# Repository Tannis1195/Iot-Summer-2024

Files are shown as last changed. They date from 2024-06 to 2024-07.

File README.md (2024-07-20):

# Tutorial on how to build an automatic plant watering system
Jonathan Lannerås (jl225yi) planned and carried out this project in June 2024.

This project is based on Raspberry Pi pico WH which reads the current soil moisture of two different plants and pumps water from a reservoir when the soil gets too dry. In addition to this, it measures: Room temperature, Sunlight, Room Humidity, and current water level in the reservoir and uploads it to an Adafruit.io dashboard through Wifi. The system is powered by a 4000mAh power bank and a 1000mAh solar-rechargeable power bank, providing a total of approximately 5000mAh and recharging when exposed to sunlight. 

While the project was completed over three weeks with sporadic effort, an average person with a basic understanding of programming and electronics could likely complete it in approximately 10 hours.

## Objective
Are you the type of person who most often forgets that plants need water? Turns out that I am, and sadly one too many cactuses has not lived to tell the tale. In plain text I'm horrible at ensuring that my green friends get the care and attention they deserve (And desperately need), therefore, it was more than time to automate myself out of the equation and give the plants a fair chance. Although this project has not dwelled as deep into network security as I initially had hoped, it has given me a lot of new insights into the realm of home automation and also gained a fascination with the relative simplicity and cheapness of deploying small IoT projects for home improvements.

The way the system is intended to work is depicted in the flowchart below: 
<div align="center">
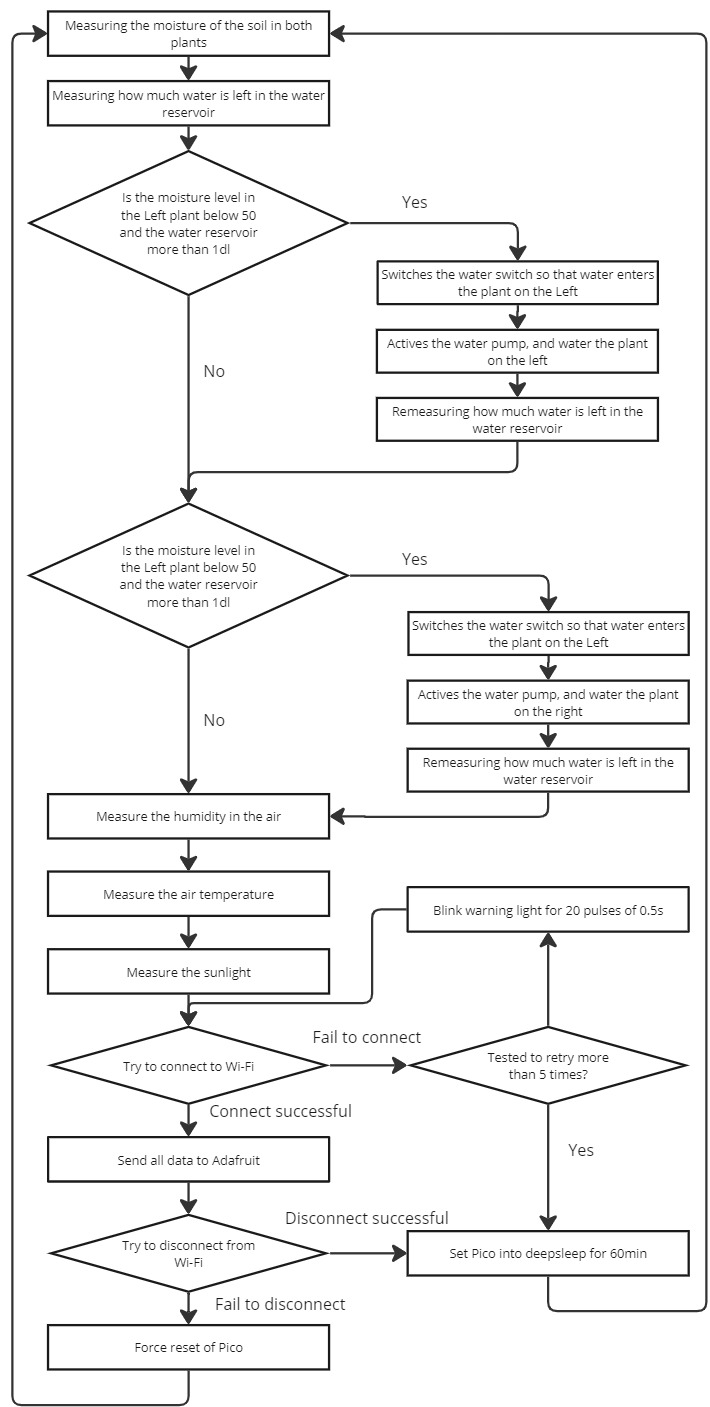
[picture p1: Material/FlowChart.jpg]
	
</div>

As seen in the flowchart the system consists of several parts and aims to both collect relevant data points, as well as continuously water the plants as needed. 

## Material

| Quantity | Component/Link | Use Case | Price (SEK) |
|---|---|---|---|
| Numerous | Just a random mix-match of childhood legos | Used to build the structure of the system | - |
| 1 | Just a large container to use as the water reservoir | Used as a water reservoir | - |
| 1 | [Male-male Wires](https://www.electrokit.com/kopplingstrad-byglar-for-kopplingsdack-mjuka-65st) | Used to connect components | 39 |
| 1 | [Male-female Wires](https://www.electrokit.com/labsladd-1-pin-hane-hona-150mm-10-pack) | Used to connect components | 29 |
| 1 | [Raspberry Pi Pico WH](https://www.electrokit.com/raspberry-pi-pico-wh) | The microcontroller used to handle all logic of the system | 109 |
| 1 | [Micro servo TS90 / SG90 1.2 kg](https://www.electrokit.com/micro-servo-ts90-sg90-1.2kg) | Micro servo used to control the water switch | 49 |
| 1 | [DHT11 Sensor](https://www.electrokit.com/digital-temperatur-och-fuktsensor-dht11) | Used to measure temperature and humidity | 49 |
| 1 | [Powerbank Keep-Alive Device](https://www.electrokit.com/powerbank-keep-alive-device) | Used to keep the powerbank from shutting off | 49 |
| 2 | [Soil Moisture Sensor](https://www.electrokit.com/jordfuktighetssensor) | Used to measure the soil moisture of the plants | 58 (total)  |
| 1 | [Red LED](https://www.electrokit.com/led-5mm-rod-diffus-1500mcd) | Used as an alarm to signal that the system failed to connect to Wi-Fi | 5 |
| 1 | [Photoresistor](https://www.electrokit.com/fotomotstand-cds-4-7-kohm) | Used to measure light level | 8 |
| 1 | [Ultrasonic Distance Sensor](https://www.electrokit.com/avstandsmatare-ultraljud-hc-sr04-2-400cm) | Used to measure water level in the water reservoir  | 59 |
| 1 | [220 ohm Resistor](https://se.rs-online.com/web/p/through-hole-resistors/0131176?gb=s) | Used for a voltage divider alongside the photoresistor | 1 |
| 1 | [Breadboard](https://www.electrokit.com/kopplingsdack-840-anslutningar) | Used to connect the different components together | 69 |
| 1 | [Relay](https://www.electrokit.com/relakort-5v-opto-isolerat) | Used to control the water pump | 49 |
| 1 | [Water Pump](https://www.electrokit.com/drankbar-pump-3v) | Used to pump water from the reservoir to the plants (Mine is 5V, but could only find a 3V; I expect similar results) | 45 |
| 1 | [Battery Pack](https://www.electrokit.com/batterihallare-4xaa-box-brytare-sladd) | Used to power the water pump (The servo and the water pump could not be on the same circuit due to the servo acting up when the pump drew power) | 29 |
| 1 | [1000 mAh Rechargeable Powerbank](https://www.dormy.com/sv/varumarken/dormy/powerbank-solar-charger-14282044fik) | Used to recharge the main powerbank | 99 |
| 1 | [Just a standard no-brand 4000mAh powerbank](https://www.netonnet.se/art/hem-fritid/el-batterier/powerbank/on-powerbank-4000-mah-1a-blue/1032352.13728/) | Used to power the breadboard and all components connected to it | ~50 |

The total cost of the entire project is difficult to accurately estimate as most of the used parts are refurbished from old Aurdino starter packs, but after finding most parts (or similar) I have calculated an estimated cost of **~800 Sek**

## Computer setup
During this project, all MicroPython code was written in the Thonny IDE. I ran Thonny on a Surface Pro 7, which was connected to the Raspberry Pi Pico via its micro USB port. Here’s how I set it up:

1. Downloaded and installed [Thonny](https://thonny.org/)
2. Hold down the BOOTSEL button (Located on the pico) while connecting the Pico to the computer (This engaged BOOTLOADER mode)
3. Open Thonny
4. Click **Run**
5. Click **Select interpreter**
6. In the dropdown list choose **MicroPython (Raspberry Pi Pico)**
7. Click **Install or update firmware** and follow the directions given in the popup window
8. Press **OK** and you are good to go!

Note that it is mandatory to test out the software in the following way: 
1. Start a new **.py** file in Thonny
2. Enter the code: <br />
`print ("Hello World")`
3. Ensure that you are using the MicroPython (Raspberry Pi Pico) as your interpreter 
4. Run the code by pressing **Run current script**
5. If all went according to plan, you should expect a nice treat in the terminal :) 

As ample guides exist on how to get Micropython installed on a Raspberry Pi Pico, I will not cover it in greater detail in this tutorial! I can, however, recommend [How to Setup a Raspberry Pi Pico and Code with Thonny](https://www.youtube.com/watch?v=_ouzuI_ZPLs), which provides an excellent and detailed walkthrough! 
## Putting everything together
The development of the project went both very well and very badly at the same time which was not all that surprising. Large portions of time went into redesigning the wiring of the system to make it as clean as possible (when looking at the wiring later, take note that it was much worse earlier). I also rebuilt the Lego structure approximately five times as the testing of the system proved more demanding than anticipated. Furthermore, I spent countless hours debugging and testing the code to ensure functionality, a major timewaster was the sporadic behavior of the "Lightsleep" function, after some digging I learned that "Deepsleep" was the way to go. Lastly, I had to redo quite a bit of work as I learned that having the pump and servo connected to the same power source was unwise when the pump started the servo started as well (For some reason), and after some digging, I learned that servos need to be run on a pretty consistent line without power fluctuation. I therefore tried to connect the servo to an external power pack but it did not wanna work therefore I hooked the pump up to the external instead and kept the servo on the 5V on the breadbord and this worked fine. But despite these hick-up most of the development rolled on quite nicely after I had gotten a costume to the technologies, case-in-point was the dashboard which was finalized an hour after I had created my Adafruit account.

### Wiring 
The wiring diagram of the project is displayed below:
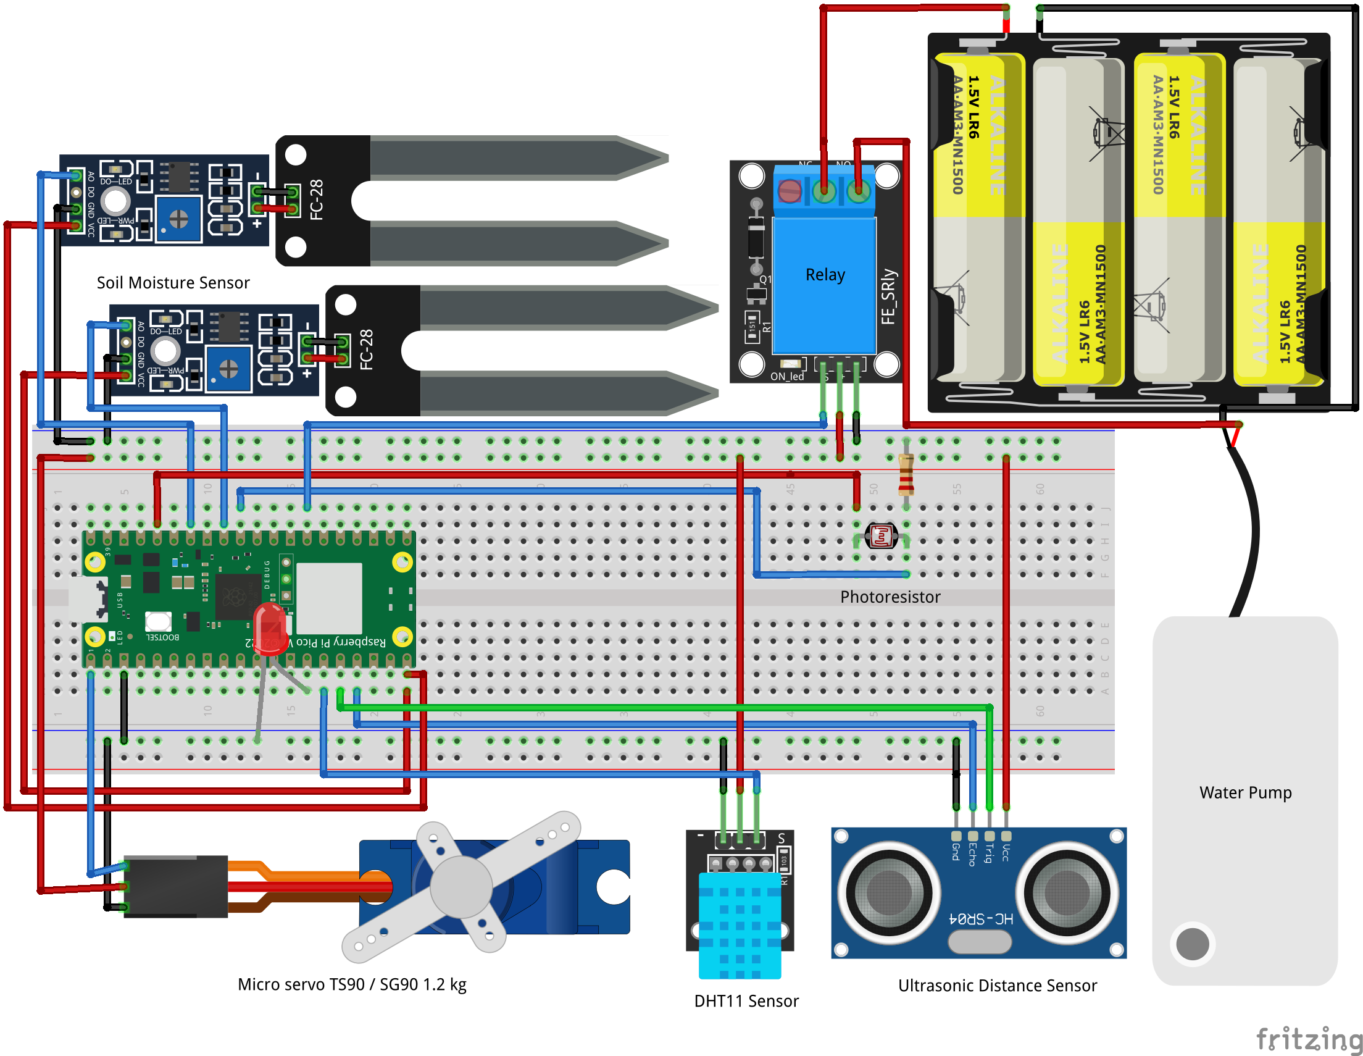
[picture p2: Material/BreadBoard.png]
Wireing diagram

In real life, this wiring is a tad bit more chaotic but it is all wired the same. The reason for my wiring work closely resembling a birds nest is that I lacked appropriate lengthed wires which led to a lot of suboptimal decisions, also the entire structure is built out of a miss match of old Lego I had laying around so the ability to plan and structure a sensible wiring approach was difficult. Thirdly, I'm also not that good at wiring so I'm certain that a more skilled practitioner who had access to the same supplies would have done more "presentable" work, but hey it works, and that's all that matters.
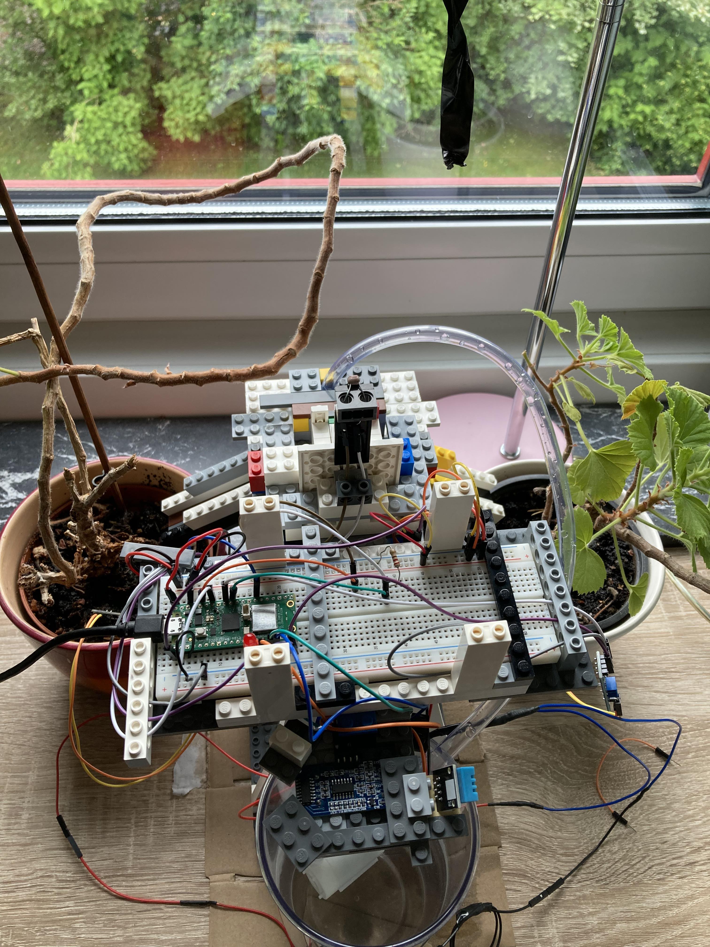
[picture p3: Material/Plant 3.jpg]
Wireing

### Power consumption 
Sadly, I could not get an accurate and long-term reading of power consumption, as I lacked access to the correct equipment. I tried to measure the current and voltage of the PICO using a multimeter and then calculate power consumption through (W = A*V), however, I was unable to get an accurate current reading of the PICO. I also tried measuring the power consumption through a wall-outlet power meter, this particular meter measures in KWh, and due to the fairly low consumption of the pico it was unable to get a reading. However, if we run some quick guesstimate for a day:

| Device | Operation Description | Duration | Current (mA) | Consumption (mAh) |
|---|---|---|---|---|
| Pico in Deepsleep | Pico in deepsleep mode (60 minutes between each of 24 readings) | 23 hours | 0.25 | 5.75 |
| Pico in action (With wifi on)  | Pico in operation (2-3 minutes for each of 24 instances) while wifi is on | 1 hour | 45 | 225 |
| Servo switch | Servo switch operation (1 activation) | 2 seconds | 500 | 0.278 |
| Water pump | Water pump operation (1 activation) | 1 second | 100 | 0.03 |
| Ultrasonic sensor HCSR0415 | Ultrasonic sensor operation (24 readings of water level) | 6 seconds | 15 | 0.025 |
| Powerbank Keep-Alive Device (active) | Powerbank wake-up pulse every 45 seconds | 192 seconds | 70 | 3.733 |
| Powerbank Keep-Alive Device (idle) | Powerbank idle state | ~24 hours | 1 | 23.947 |
| Soil moisture readings (per sensor) | Soil moisture sensor operation (24 readings per sensor) | 720 seconds | 15 | 3 (per sensor) |
| DHT11 sensor | DHT11 sensor operation (24 readings of temperature and humidity) | 2.4 seconds | 2.5 | 0.002 |

If we sum these estimates up we land at around 300 (~265) mAh per day. Given that I have around 5000 mAh in powerbank (without recharge) this indicates around 19 days of usage before having to recharge, which from experience seems probable but optimistic.     

## Platform 
In this project, all data is transmitted and stored in [Adafruit.io](https://io.adafruit.com/). My reasoning for choosing Adafruit instead of other options was based on two factors: Cost and ease of use. First of all, Adafruit is free to a limited extent and given the relatively low amounts of data I'm transmitting I was able to operate within these limits. Secondly, the ease of sending data to Adafruit using API made this a very attractive alternative as I'm familiar with how APIs work and was comfortable sending the data this way. Additionally, the way Adafruit has chosen to structure incoming data using different "feeds" which then can be used within dashboards was very straightforward and user-friendly, which was greatly appreciated on my part. It should, however, be noted that I found the free version of Adafruit to be quite limited in terms of data analytics and data representation but given the rather basic nature of the project, the need for either is close to non-existent. It would, however, have been neat to run a forecasting model on the data to determine when at what time the next refill of the water reservoir is bound to happen. This can of course be presumed offline by downloading the uploaded data from Adafruit and inputting it into analytical software such as **R** or **Python**. Additionally, using the free version of Adafruits services greatly impairs the scalability of the project as one is limited to 10 feeds in total, and currently the project is at 7 meaning that 3 additional plants could get added (Given that they are near the other plants) before one runs out of feeds.   <br />

Furthermore, my decision to use Adafruit in this project was also driven by the fact that I wanted to try out a cloud-based approach to IoT, and this project seemed like a good starting point. Why I deemed this project appropriate because of the fairly non-sense data I'm transmitting, for instance, I'm not transmitting live audio and video of my living room, because if this data leaks or gets intercepted the attacker will only gain some very detailed info about a mismanaged houseplant (and I can live with that).   
## The code
The core function within my code, the beating heart so to speak, is my main loop. The main loop executes my entire program and loops indefinitely, initially, the main loop addresses data collection and the watering functionalities of the system, after this the function shifts focus towards the uploading of the collected data to Adafruit. Not that if the program fails to connect to the internet, it will simply discard the collected data and enter deepsleep, this was an active choice of mine as the core functionality of the system is not the uploading of plant data to the internet, it is the ensuring of having the plants watered.   

```python
def main():
    while True:
        alarm_Pin.value(0) # Sets alarm pin to off 
        moist = plant_Monitor (sensorVCC,[left_Soil_Sensor,right_Soil_Sensor]) # Calculate the moisture level of the plants
        plant_Left_Moist_Level = moist[0]
        plant_Right_Moist_Level = moist[1]
        plants =[
            ["left",plant_Left_Moist_Level,50],
            ["right",plant_Right_Moist_Level,50]
        ]
        water_Level, watering = watering_Of_Plants(plants) # Calculates the water level in the water tank and investigates if the plants need to be watered   
        humidity_Temp = humidity_Temp_Tracker(25) # Calculates both Tempature and Humidity data
        temperature = humidity_Temp[0]
        humidity_Level = humidity_Temp[1]
        sun_Light = light_Tracker(50) # Calculates the current light level
        print("Moisture level of the Left plant: ", plant_Left_Moist_Level, "\n",
              "Moisture level of the Right plant: ", plant_Right_Moist_Level, "\n",
              "Temperature: ", temperature, "\n",
              "Humidity: ", humidity_Level, "\n",
              "Light Level: ", sun_Light, "\n",
              "Water Level: ", water_Level, "\n",
              "Watering events: ", watering)
         
        connected, wlan = connect_To_Wifi() # Try to connect to Wifi
        if connected:
            #Send data to Adafruit
            send_To_Adafruit(plant_Left_Moist_Level, "moisture-plant-1")
            plant_Left_Moist_Level=None #Delete from memory
            send_To_Adafruit(plant_Right_Moist_Level, "moisture-plant-2")
            plant_Right_Moist_Level=None #Delete from memory
            send_To_Adafruit(water_Level, "water-tank")
            water_Level=None #Delete from memory
            send_To_Adafruit(temperature, "temperature")
            temperature=None #Delete from memory
            send_To_Adafruit(humidity_Level, "humidity")
            humidity_Level=None #Delete from memory
            send_To_Adafruit(sun_Light, "sun-light")
            sun_Light=None #Delete from memory
            if len(watering) != 0: # If a watering event has been recorded
                for i in watering:
                    send_To_Adafruit(i,"watering-event")
                watering=None #Delete from memory
            wlan.disconnect() # Disconnect from WIFI
            time.sleep(1)
            if wlan.isconnected(): #If unable to disconnect
                print ("Disconnect has failed :(, It left me no choice")
                machine.reset() # Hard reset, im not allowing the pico to keep wifi on under any circumstance
            else:
                print("Great success, we have disconnected!")
                
        else: # If unable to connect to Wifi
           print("Connection was never an option :(, Data not delivered") # Data do not get uploaded or stored (Main objective is to ensure plant safety not Dashbord uplink)
           alarm_Pin.value(1) # Turn on alarm pin to indicate error
               
        deepsleep(60*60*1000)#Puts the pico into deepsleep for 60min
```
In all honesty, the majority of the code is centered around the collection of data from different sensors this is code that already has ample literature online and therefore is quite boring to address but I do have three codes that are a bit more interesting to look at.
### Deletion of outliers 
Albit, using a function that cleans the data from outliers is not a revolutionary concept nor unusual to include, the function is however usually imported from an established library rather than written. This was the first time I wrote such a function myself and it could be fun to share, especially as it is beyond important when dealing with sketchy wiring and sensors which are prone to throw out a strange value more often than not. The function incorporates linear interpolation when calculating the quartile values of Qurtial 1 and 2, these are then used to calculate the interquartile range and the lower and upper bounds. These bounds act as borders, any values beyond them are excluded leading to a clean dataset.   
```python
def outlier_Deleter(value_Array):
    value_Array = sorted(value_Array)
    n = len(value_Array)
    q1_Pos = (n + 1) / 4
    q3_Pos = 3 * (n + 1) / 4
    # This function is used to calculate the quartile values
    def qurtile_calc(pos):
        lower = value_Array[int(pos)-1]
        upper = value_Array[int(pos)]
        return lower + (pos%1)*(upper - lower)
    q1 = qurtile_calc(q1_Pos) # quartile 1
    q3 = qurtile_calc(q3_Pos)# quartile 1
    iqr = q3-q1# inter quartile range
    lower_Bound = q1 - (1.5*iqr)
    upper_Bound = q3 + (1.5*iqr)
    filtered_array = list(filter(lambda x:lower_Bound<=x<=upper_Bound,value_Array))
    return filtered_array
```

### Tracking Water level using an Ultrasonic Distance Sensor
This is the function used to determine the current level of water in my water reservoir/tank, it uses an Ultrasonic Distance Sensor mounted over the reservoir. It works by measuring the time it takes for a pulse to hit the water and then bound back to the Sensor, then converting this pulse time to get the gap between the sensor and water in centimeters. When the gap is determined I use this information to determine how much water I got in the reservoir, if there is no gap between water and sensor I got 9,4 dl and for every centimeter of the gap, the amount decreases by 0.56 DL meaning that when the gap is 16,8 cm the reservoir is empty!   
```python
def water_Level_Reader(sample_Size):
    result_Array = []
    for i in range(sample_Size):
        trig_SoundSensor.value(0)
        time.sleep(0.005)
        trig_SoundSensor.value(1)
        time.sleep(0.00001)
        trig_SoundSensor.value(0)
        pulse_time = time_pulse_us(echo_SoundSensor, 1, 500*2*30) #Records the pulse time of the Ultrasonic Distance Sensor
        if not (pulse_time < 0): # If the pulse time is more than 0 (Remove noise) 
            result_Array.append(pulse_time)
        
    clean_result_Array = outlier_Deleter(result_Array) # Clean the pulse data from outliers 
    result_Array = None # Remove result array to save on memory
    average_pulse_time = sum(clean_result_Array)/len(clean_result_Array) # Calculate the average pulse time
    cms = (average_pulse_time / 2) / 29.1 # Convert pulse time to centimeters (Distance between sensor and water level)
    water_volume = -0.56 * cms + 9.4 # Convert centimeters to Water quant in DL (My tank is a slight cone shape therefore the need for a function) 
    gc.collect()  # Delete nonsense data, Keep memory free!
    return water_volume
```
For the interested reader, I have also submitted the complete code [Here](https://github.com/Tannis1195/Iot-Summer-2024/blob/main/Material/main.py).
### Running a  Micro servo TS90 / SG90 1.2 kg without a ADC pin
The last bit of code I would like to showcase was about to be my show stopper. When having installed all the equipment I chose to expend a bit on my scoop and create a switch that regulated the water flow, however, I had a problem, because I wanted to control this switch using a servo and I had run out of ADC pins which on usually use to run servos. However, after a bit of tinkering and searching, I learned that one can use the normal GPIO pins to run a servo by mimicking the correct 50hz signal, which was quite an intriguing task. So on a high level, you determine how long a pulse needs to be (20ms in this case, 1/operating frequency), then you figure out how long of this pulse the value should be high and how long it should be low, then you run this pulse for the desired frequency (in this case 50hz, which the servo operates at). As you can see I chose not to run my servo to the extremes (0 and 180) as I did not want to risk damaging the servo if the calculations were off and the servo ended up outside the operating range.   
```python
def set_switch(direction):
    # As I ran out of ADC pins I had to run the servo manually instead of the normal way, not ideal but it gets the work done
    hz = 50 # The Hz the server operates at
    puls_Period = 1/hz #  The puls period at 50Hz is 20ms(0.02s)
    if direction == "left":
        servo_pos = 20 # Not going to 0 as to make sure I'm not over-shooting and damaging the servo (I'm not sure of the precision of controlling the servo this way)
    else: # If the right plant is the one to be watered
        servo_pos = 160 # Not going to 180 as to make sure I'm not over-shooting and damaging the servo (I'm not sure of the precision of controlling the servo this way)
    pulse = 0.0005 + (servo_pos/180)*0.0019 # 0.5ms for 0 degree, 1.9ms + 0.5ms = 2.4ms for 180 degree
    for _ in range(hz): ## the servo operates at 50Hz a second
        water_Switch_pin.value(1)
        time.sleep(pulse) 
        water_Switch_pin.value(0)
        time.sleep(puls_Period-pulse)
    gc.collect()  # Delete nonsense data, Keep memory free!
```

## Transmitting the data / connectivity
I use the Adafruit platform to both store and visualize my data, given that I'm monitoring plants the need for all too frequent updates was deemed unnecessary therefore transmittions occur once every hour. In this project, I chose to use Wifi as the wireless protocol. The reasoning behind this was that the project was launched in my private residence which has WiFi, therefore the use of more sophisticated methods seemed a bit extreme especially as there was no TTPs coverage nor any helium hotspots where I lived, which means I would have needed to invest in LoRaWAN equipment, which in all honesty seemed overkill for this deployment. I mentioned earlier that one key selling point for using Adafruit was the ability to send data using APIs, this is something that is achieved using HTTP/HTTPS as a transport protocol, in greater detail, I'm using HTTP post requests to deliver my data to the Adafruit server. One drawback of sending the data to Adafruit in this manner is that one can only send one data value at a time, meaning that one can not group all data and send it through post request instead you have to send one post request for each data point you want to upload, which consumes more energy. On the topic of energy, it should be noted that my decision to use WiFi had a fairly significant impact on the battery, however, as the WiFi is disconnected directly after the transmission is finalized thereby, power consumption is minimized.  <br />

Additionally, a decision taken by me was that the connection was only established one way, meaning that I sent data to Adafruit but Adafruit was unable to send data back. This impairs my ability to control anything on the pico over the internet using Adafruit, like watering a plant by pressing a button. Although this could be seen as a bit limiting it serves several purposes, first this is an automatic watering system and there should never occur a situation where I need to interact with the system over the internet. Secondly, if I were to be able to interact with the system over Adafruit I would need to be uplinked to Wifi constantly, which would drain far too much power. Thirdly, having a PICO constantly uplinked to the internet seems like an unnecessary risk as it is a possible point of attack against my network which I do not favor, I have on the other hand placed the PICO on its own VLAN as a security precaution but better safe than sorry.  
## Presenting the data
As previously mentioned, I'm using the Adafruit platform to both, store and visualize the data. The data is transmitted to Adafruit once every hour. Using Adafruit for this purpose is well suited for my project as Adafruit allows me to save 1KB in each feed for 30 days, the 30 days of storage is plenty given the needs of the project, however, the 1KB of storage is on the low side as all my data transitions are around 8 bytes each meaning that I have around five days of transmission before I reach the cap. However, as I'm not performing any data analytics on past data, this is not a major problem in this project. In the picture below I display how I have structured my Adafruit.Io dashboard:
<div align="center">
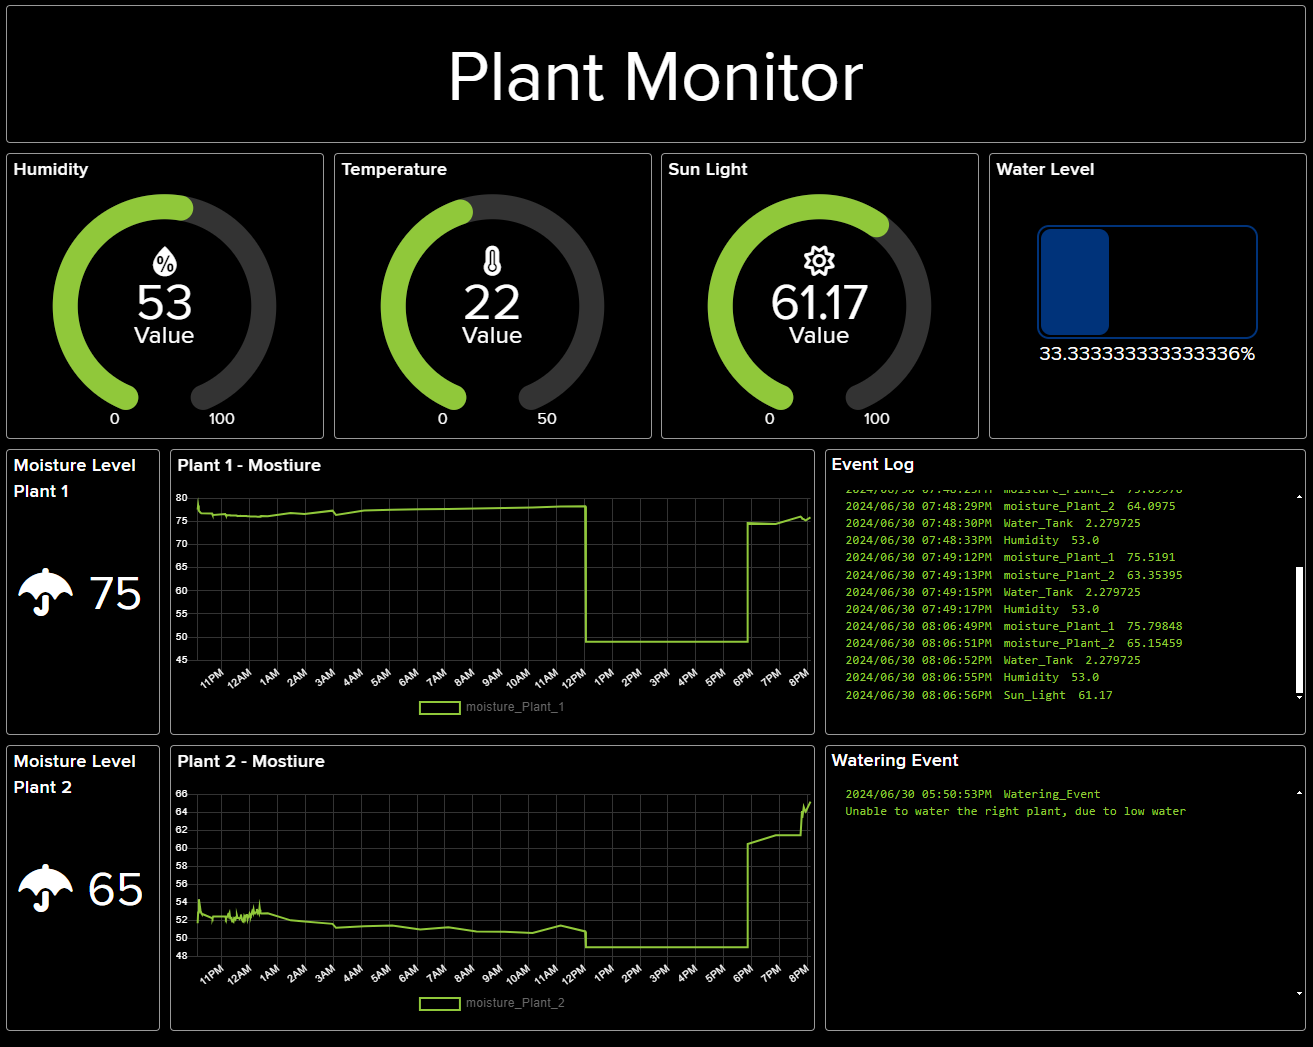
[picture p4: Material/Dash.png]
	
</div>
I have structured the dashboard to quickly convey the data to the user. Firstly, for all measurements, I'm conveying the current state both numerically and graphically. Secondly, for the soil moisture, I'm also including a line graph highlighting how the soil moisture level has developed, giving a more detailed oversight on this data is obvious as the entire system is centered around ensuring the well-being and watering of the plants. Thirdly, I have also attached a terminal that displays the raw data that has been incorporated from the different feeds and when this data was uploaded to the dashboard, which provides the user with an understanding of the freshness of the data. Lastly, a terminal displaying information regarding watering events is also present in the dashboard, which informs a user regarding past watering events (Eg. if a plant has been watered or if a plant should have been watered but the reservoir was too low). All in all, I believe the dashboard provides adequate insight into the current situation of the plants, without drowning the user in data.  I mentioned earlier that I am not allowing Adafruit to send data back to the PICO meaning which explains why the dashboard lacks any interactive features, such as buttons or sliders, however, I do not feel like these would add much to the user experience in this case.

## Finalizing the design
After many hours, more than I want to admit, I was able to finalize my build. I must admit that I have seen more aesthetically pleasing lego builds in my life, however, I'm more of a function-oriented person, and I'm quite satisfied with how it works. 

<div align="center">
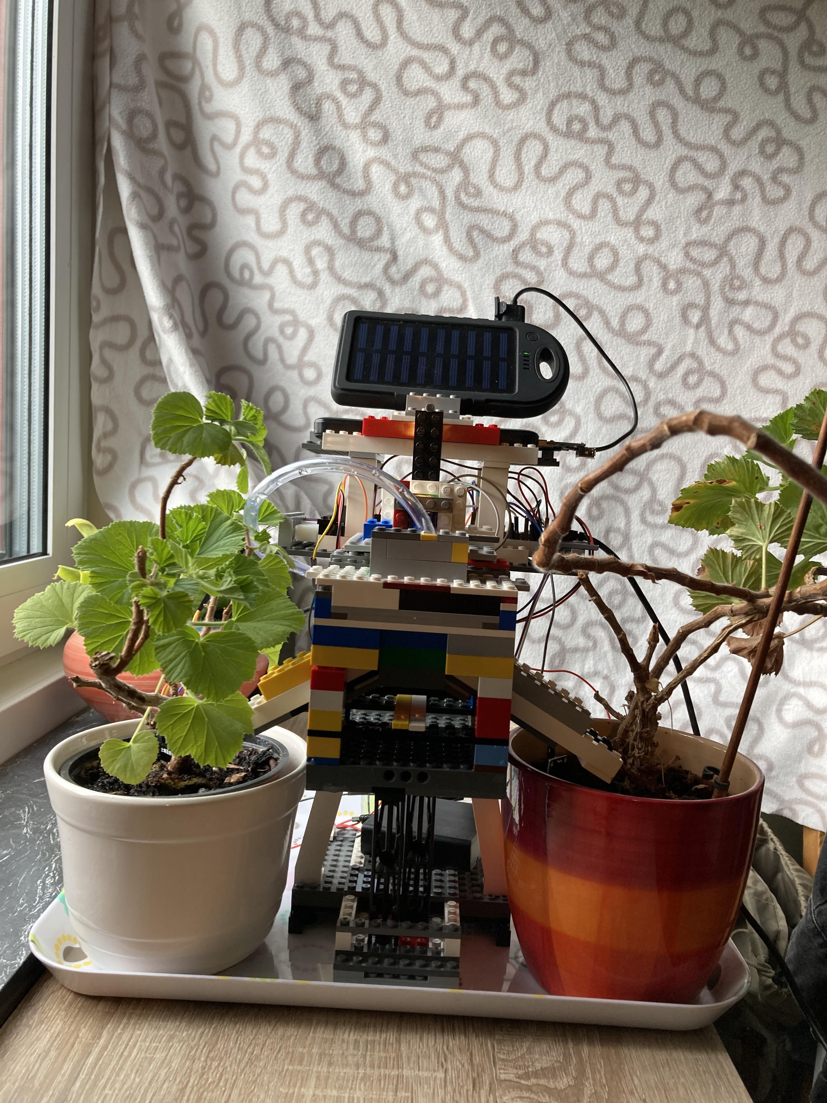
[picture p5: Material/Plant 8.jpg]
	
</div>

<div align="center">
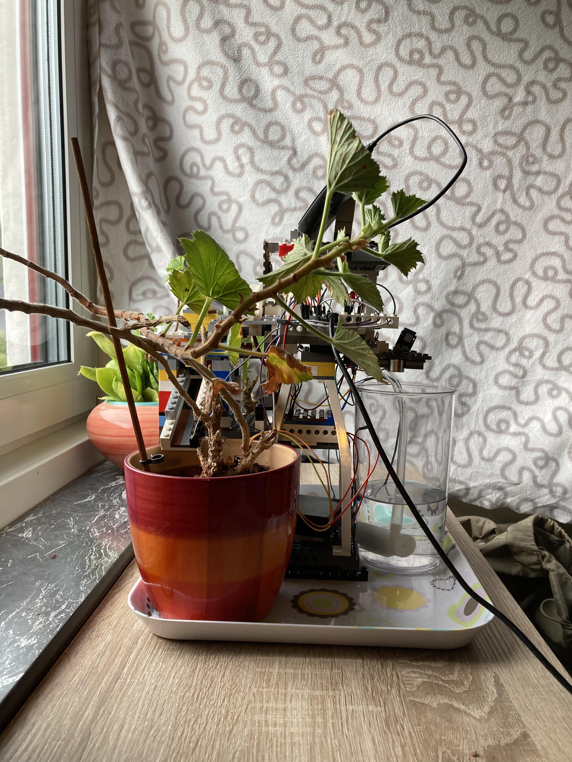
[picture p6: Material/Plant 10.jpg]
	
</div>

<div align="center">
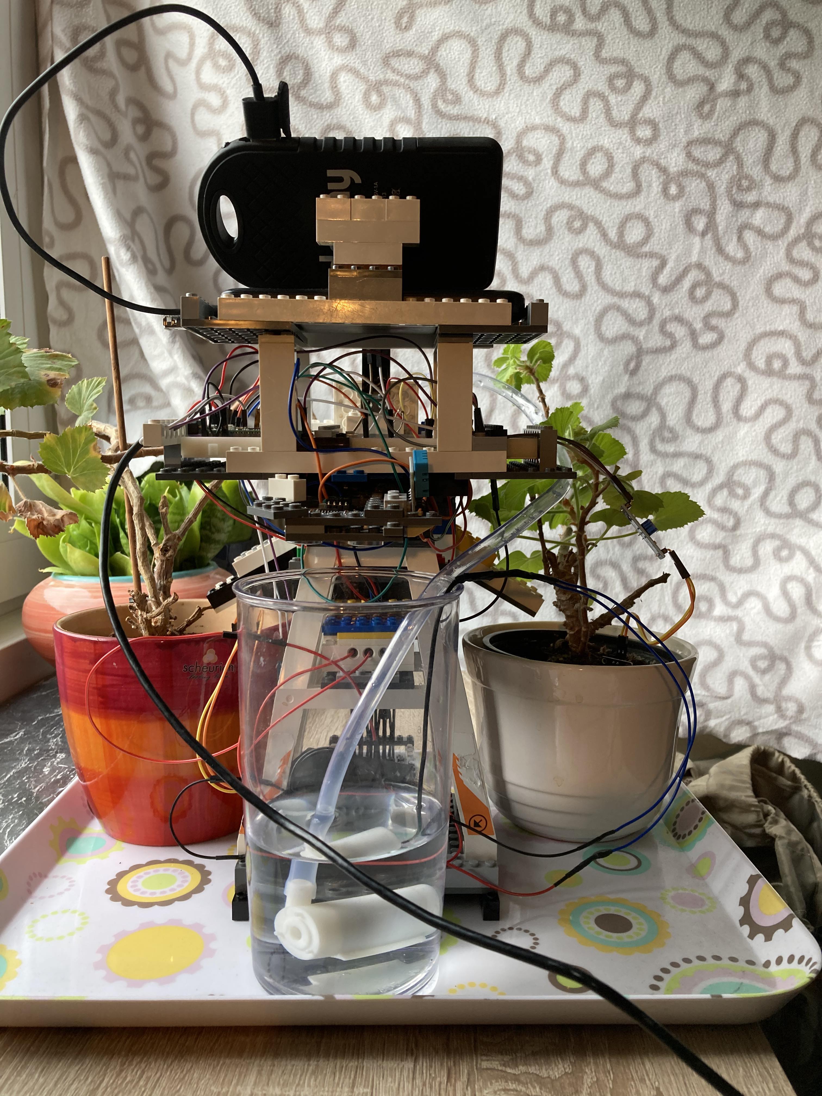
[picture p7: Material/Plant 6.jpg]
	
</div>

<div align="center">
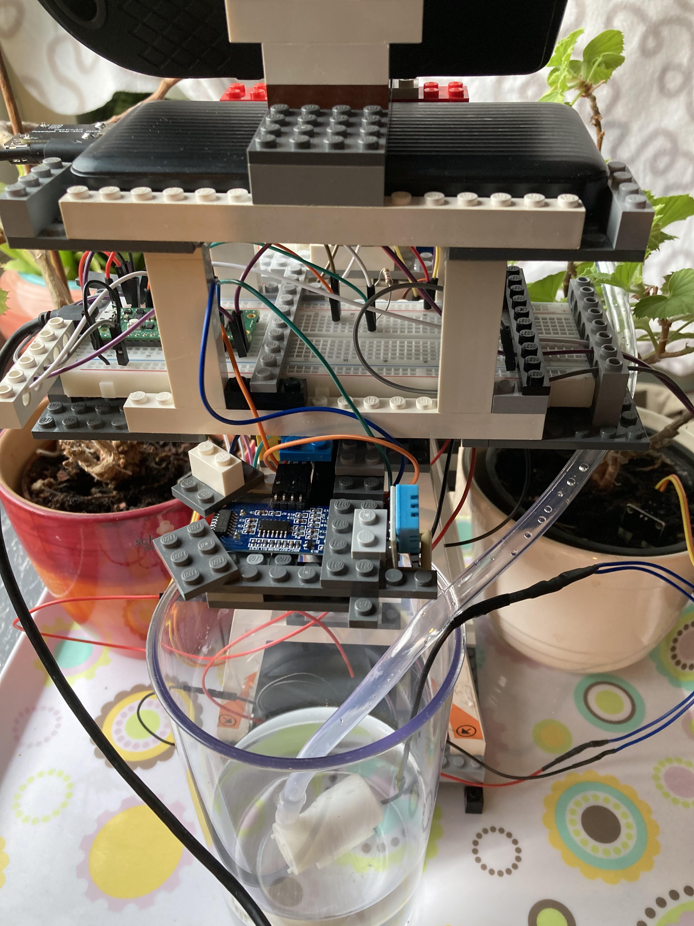
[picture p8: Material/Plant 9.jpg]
	
</div>

<div align="center">
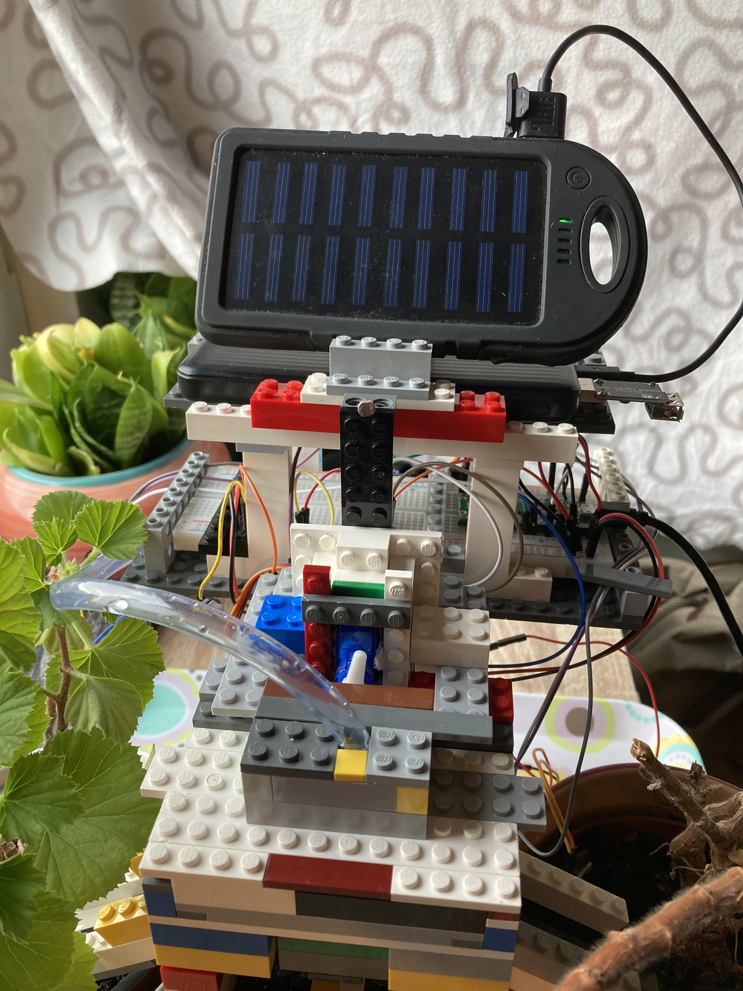
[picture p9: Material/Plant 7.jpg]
	
</div>

As I'm not exactly aware when the watering will take place I hard coded in that both plants needed water to be able to record the video below showcasing the system in action :) (The dedicated viewer can see that a little bit of water always escape in to the other plant, this is because the lego seal is not exactly submarine rated) 

<div align="center">
    <a href="https://www.youtube.com/watch?v=nqmDZlCsAVM">
        Watering Session Video
    </a>
</div>

Additionally, for me, this project is only viewed as an early version of an automated plant watering system and is something that I will continue to develop in the future. The currently assembled project is not home decor at its finest and is likely to be disabled soon as to reuse the parts in my V2!

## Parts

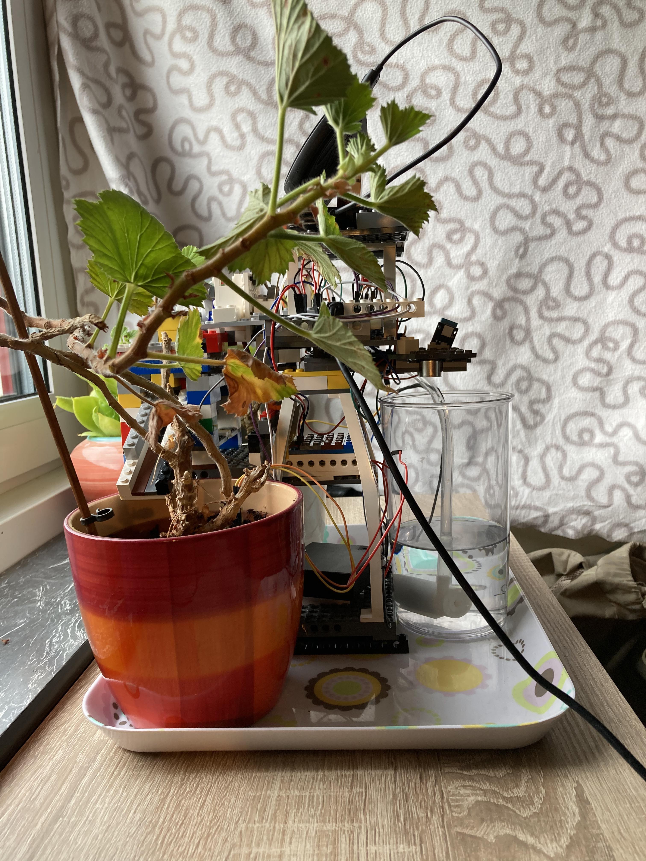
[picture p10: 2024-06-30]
Material/Plant 5.jpg

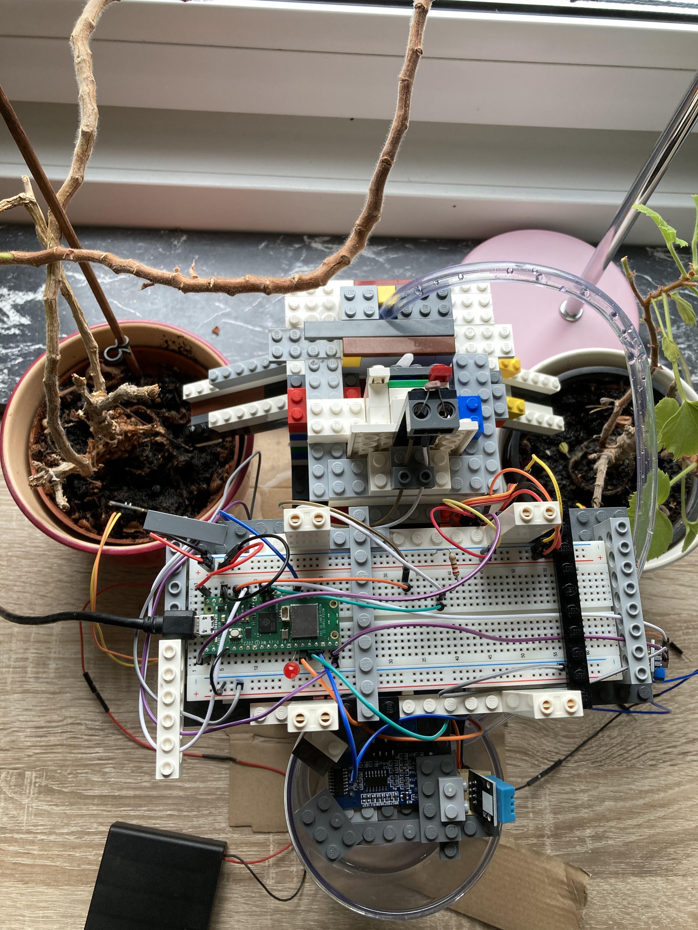
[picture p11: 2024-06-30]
Material/Plant 4.jpg

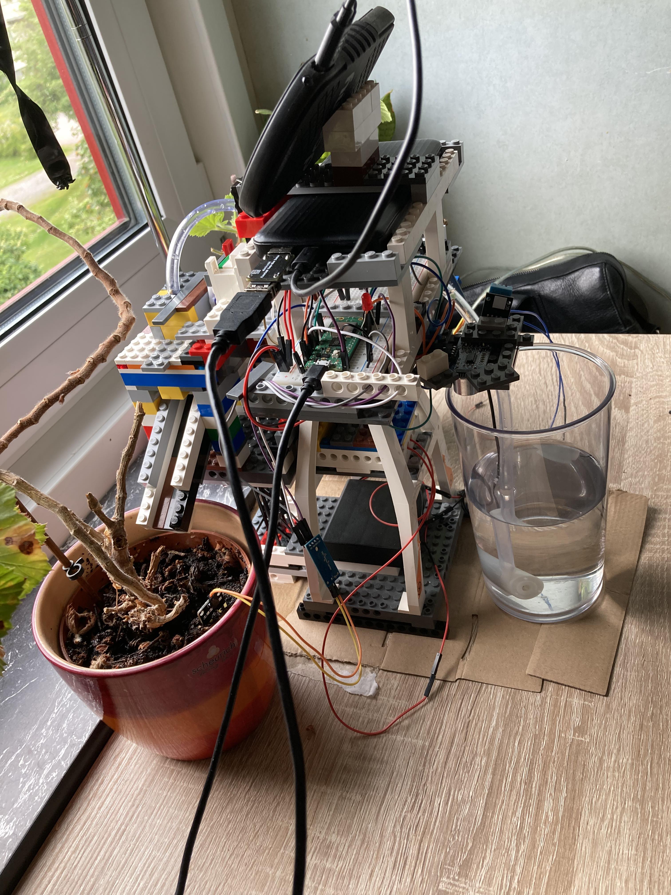
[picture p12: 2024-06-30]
Material/Plant 2.jpg

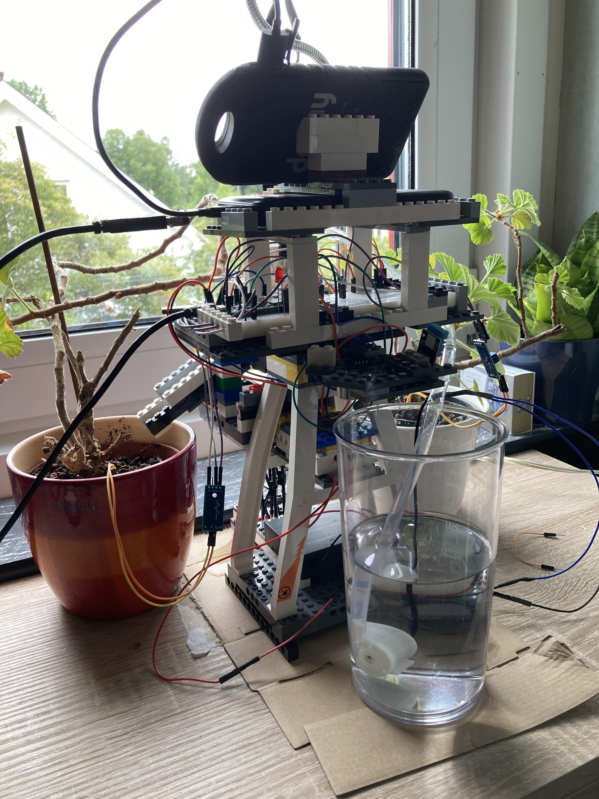
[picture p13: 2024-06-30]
Material/Plant 1.jpg

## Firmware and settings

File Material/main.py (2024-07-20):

from machine import Pin, ADC, time_pulse_us,deepsleep
import time
import network
import urequests
import dht
import gc 

### ---------- Setting pins -------------------
pump_relay = Pin(21,Pin.OUT) # Pin which is connected to the water pump 
water_Switch_pin = Pin(0, Pin.OUT) # Pin which is connected to the Servo 
alarm_Pin = Pin(10,Pin.OUT) # Pin which connected to the alarm Led
humidity_Sensor = dht.DHT11(Pin(11)) # Pin which is connected to the DHT11 sensor
trig_SoundSensor = Pin(12,Pin.OUT) # Pin which is connected to the trig pin of the Ultrasonic Distance Sensor
echo_SoundSensor = Pin(13,Pin.IN)# Pin which is connected to the echo pin of the Ultrasonic Distance Sensor
sensorVCC = Pin(15, Pin.OUT) # Power to mostiure Sensors
light_Reader = ADC(Pin(26))# Pin which is connected to the Photoresistor
right_Soil_Sensor = ADC(Pin(27)) # Read value from mostiure Sensor in the right plant 
left_Soil_Sensor = ADC(Pin(28)) # Read value from mostiure Sensor in the left plant 

### ---------- Support functions -------------------
# This function is used to clean an array of outliers (Bad values)
def outlier_Deleter(value_Array):
    value_Array = sorted(value_Array)
    n = len(value_Array)
    q1_Pos = (n + 1) / 4
    q3_Pos = 3 * (n + 1) / 4
    # This function is used to calculate the quartile values
    def qurtile_calc(pos):
        lower = value_Array[int(pos)-1]
        upper = value_Array[int(pos)]
        return lower + (pos%1)*(upper - lower)
    q1 = qurtile_calc(q1_Pos) # quartile 1
    q3 = qurtile_calc(q3_Pos)# quartile 1
    iqr = q3-q1# inter quartile range
    lower_Bound = q1 - (1.5*iqr)
    upper_Bound = q3 + (1.5*iqr)
    filtered_array = list(filter(lambda x:lower_Bound<=x<=upper_Bound,value_Array))
    return filtered_array
### ---------- Uploading to Adafruit functions -------------------
# This function is used to connect the pico to wifi
def connect_To_Wifi():
    wlan = network.WLAN(network.STA_IF)
    wlan.active(True)
    connection_wait = 10 # How long im allowing the connection to take
    connection_Fails = 0 # Index used to keep track of how many times connection failed
    max_Connection_Tries = 5 # How many failes I allow
    while connection_Fails < max_Connection_Tries: # Runs till the max number of connection attemps has been reached
        initiation_Start_Time = time.time()
        wlan.connect("ENTER YOUR ssid HERE","ENTER YOUR password HERE") # Please create a .py file called secrets and place these credentials there and retrive them this way: secrets["ssid"],secrets["password"]
        while not wlan.isconnected(): # Runs till connected to Wifi
            if time.time() - initiation_Start_Time > connection_wait: # If connection is not made in a timly manner
                connection_Fails +=1
                print("Connection failed :(")
                for _ in range(20): # Runs a blinking led to indicate failiure
                    alarm_Pin.value(1)
                    time.sleep(0.5)
                    alarm_Pin.value(0)
                    time.sleep(0.5)
                break #Exit While loop
            time.sleep(0.5)
            
        if wlan.isconnected(): # If a connection was made
            break
        
    return wlan.isconnected(),wlan # 
# This function is used to send data to a Adafruit stream
def send_To_Adafruit(data, feed):
    adafruit_API_URL = "https://io.adafruit.com/api/v2/{}/feeds/{}/data".format("INSERT YOUR aio_username HERE", feed) # Sets API link | Please create a .py file called secrets and place these credentials there and retrive them this way: secrets["aio_username"]
    headers = {"Content-Type":"application/json","X-AIO-Key":"INSERT YOUR aio_key here"} # Defining headers of API post | Please create a .py file called secrets and place these credentials there and retrive them this way: secrets["aio_key"]
    data = {"value":data} # Creating Json
    try:
        adafruit_Response = urequests.post(adafruit_API_URL, json = data, headers = headers) # HTTP post requests
        if adafruit_Response.status_code == 200: # If data transmission was sucessful 
            print ("Mission control: Data handover was a success")
        else: # If not 
            print("Huston we had a problem: ", adafruit_Respons.status_code)
            print(adafruit_Respons.text)
    
    except Exception as error: # If an error occure 
            print ("Huston we had a RequestException error: ",error)
    gc.collect() #Delete nonsense data to preserve memory!
### ---------- Soil functions -------------------
# Function used to transform the Raw moisture value into a precentage between 0-100
def moisture_Precent(curr_Val):  
    dry_Soil_Value = 65535 # Max value, The high seas 
    wet_Soil_Value = 0 # Min value, Desert 
    percent = (curr_Val - dry_Soil_Value) * (100) / (wet_Soil_Value - dry_Soil_Value)
    return round(percent, 2)

# Function used to collect the moisture value in each plant
def read_Sensor_Average(samples, plant_Reader, plantVCC):
    total = []
    return_Array = []
    for _ in range(samples): # Run samples time
        plantVCC.value(1)  
        time.sleep(0.005)
        single_Mesure_Array = []
        for sensor in plant_Reader: # Loop over all plants
            single_Mesure_Array.append(sensor.read_u16()) # Create array [Value plant1, Value plant2,...]
        total.append(single_Mesure_Array) # Create array [[Value plant1, Value plant2,...],[Value plant1, Value plant2,...]]
        plantVCC.value(0)  
        time.sleep(0.005)
    for i in range(len(plant_Reader)):# Loop over the number of plants 
        clean_Value_array = outlier_Deleter([row[i] for row in total]) # Take out the values associate with the plant and clean the array from outliers
        moisture = moisture_Precent(sum(clean_Value_array) / len(clean_Value_array)) # Send the average value of the raw values to calculate the precentage between 0-100
        return_Array.append(moisture) # Append mosture level to retrun array [Moist_Level_Plant_1, Moist_Level_Plant_2,...]
    gc.collect()  # Delete nonsense data, Keep memory free!
    return return_Array

# Function used to collect the mean moisture value in each plant
def plant_Monitor (plantVCC,sensorArray):
    sampleSize = 50
    moistureData = []
    return_Array = []
    for _ in range (sampleSize): #As the mesurmement of soil is noizy I collect 50 moisture value per plant
        plant_moist_Value = read_Sensor_Average(sampleSize,sensorArray, plantVCC) # Collect moisture value
        moistureData.append(plant_moist_Value)
  
    for i in range(len(sensorArray)):
        moisture_Plant = outlier_Deleter([row[i] for row in moistureData]) # Take out the values associate with the plant and clean the array from outliers
        moisture = sum(moisture_Plant) / len(moisture_Plant) # Calculate the mean value of the clean array
        return_Array.append(moisture) # Append mosture level to retrun array [Mean_Moist_Level_Plant_1, Mean_Moist_Level_Plant_2,...]
    gc.collect()  # Delete nonsense data, Keep memory free!
    return return_Array


### ---------- Watering functions -------------------
# This function is used to measure how much water there is in the water tank
def water_Level_Reader(sample_Size):
    result_Array = []
    for i in range(sample_Size):
        trig_SoundSensor.value(0)
        time.sleep(0.005)
        trig_SoundSensor.value(1)
        time.sleep(0.00001)
        trig_SoundSensor.value(0)
        pulse_time = time_pulse_us(echo_SoundSensor, 1, 500*2*30) #Records the pulse time of the Ultrasonic Distance Sensor
        if not (pulse_time < 0): # If the pulse time is more than 0 (Remove noise) 
            result_Array.append(pulse_time)
        
    clean_result_Array = outlier_Deleter(result_Array) # Clean the pulse data from outliers 
    result_Array = None # Remove result array to save on memory
    average_pulse_time = sum(clean_result_Array)/len(clean_result_Array) # Calculate the average pulse time
    cms = (average_pulse_time / 2) / 29.1 # Convert pulse time to centimeters (Distance between sensor and water level)
    water_volume = -0.56 * cms + 9.4 # Convert centimerters to Water quant in DL (My tank is a slight cone shape therefor the need of a function) 
    gc.collect()  # Delete nonsense data, Keep memory free!
    return water_volume

# This function controls the water pump 
def water_distribution (plant):
    set_switch(plant) # Sets the switch so the water flows to the correct plant
    time.sleep(2) # Ensure switch has happen
    pump_relay.value(1)
    time.sleep (1) # Pump is on for 1s which is plenty of water
    pump_relay.value(0)
    time.sleep(2) # Ensure all water is through

# This function is used to control the servo which regulates to which plant the water flows
def set_switch(direction):
    # As I ran out of ADC pins i had to run the servo manually instead of the normal way, not ideal but it gets the work done
    hz = 50 # The Hz the server operates at
    puls_Period = 1/hz #  The puls period at 50Hz is 20ms(0.02s)
    if direction == "left":
        servo_pos = 20 # Not going to 0 as to make sure im not over-shooting and damaging the servo (I'm not sure of the precision of controlling the servo this way)
    else: # If the right plant is the one to be watered
        servo_pos = 160 # Not going to 180 as to make sure im not over-shooting and damaging the servo (I'm not sure of the precision of controlling the servo this way)
    pulse = 0.0005 + (servo_pos/180)*0.0019 # 0.5ms for 0 degree, 1.9ms + 0.5ms = 2.4ms for 180 degree
    for _ in range(hz): ## the servo operaters at 50Hz a second
        water_Switch_pin.value(1)
        time.sleep(pulse) 
        water_Switch_pin.value(0)
        time.sleep(puls_Period-pulse)
    gc.collect()  # Delete nonsense data, Keep memory free!
 
# This function is used to determine if the plants need watering and if so waters them. 
def watering_Of_Plants(plants):
    water_Level  = water_Level_Reader(50) # Determines current water level in water tank
    watering_Activity = []
    for plant_Info in plants: # Loops over all plants
        plant = plant_Info[0] # Retrives what plant (Left plant, right plant, etc) 
        plant_Moist_Level = plant_Info[1] # Retrives the measured moisture level of the plant
        threshold_Value = plant_Info[2] # Retrives moisture threshold value of said plant 
        safe_Water_Level = 1 # Running the pump without water is wasteful and dry running can damage the pump
        
        if plant_Moist_Level < threshold_Value: # If the plant needs to be watered
            if water_Level>safe_Water_Level: # Is there enough water in the tank?
                water_distribution(plant) # Water the plant
                watering_Activity.append("The " + plant + " plant was watered")
                water_Level  = water_Level_Reader(50) # Redetermine current water level in water tank
            else: 
                watering_Activity.append("Unable to water the " + plant + " plant, due to low water")
    gc.collect()  # Delete nonsense data, Keep memory free!
    return water_Level,watering_Activity

### ---------- Additional data functions -------------------
# This function is used to calculate the current light level
def light_Tracker(sample_Size):
    result_Array = []
    for i in range(sample_Size):
        result_Array.append(light_Reader.read_u16()) #Collects sample_Size light readings
    clean_result_Array = outlier_Deleter(result_Array) # Cleans the collected readings from outliers
    result_Array = None #Removes old array to save on memory
    curr_Val = sum(clean_result_Array)/len(clean_result_Array) # Calculate mean
    
    dark_Value  = 100 # The darkest value I have recorded in my room was 300
    sun_Value = 50000 # The brights value I have recorded in my room was 45000
    percent = (curr_Val - dark_Value) * (100) / (sun_Value - dark_Value) # Convert to a scale 0-100
    gc.collect()  # Delete nonsense data, Keep memory free!
    return round(percent,2)
# This function is used to calculate both the humidity and Tempature 
def humidity_Temp_Tracker(sample_Size):
    result_Temp_Array = []
    result_Humidity_Array = []
    for i in range(sample_Size):
        humidity_Sensor.measure() # The DTH11 collects both Tempature and Humidity data
        result_Temp_Array.append(humidity_Sensor.temperature())
        result_Humidity_Array.append(humidity_Sensor.humidity())
        
    clean_result_Temp_Array = outlier_Deleter(result_Temp_Array) # Cleans the collected readings from outliers
    clean_result_Humidity_Array = outlier_Deleter(result_Humidity_Array)# Cleans the collected readings from outliers
    result_Temp_Array = None #Removes old array to save on memory
    result_Humidity_Array = None #Removes old array to save on memory
    
    curr_Val_Temp = sum(clean_result_Temp_Array)/len(clean_result_Temp_Array) # Calculate mean
    curr_Val_Humidity = sum(clean_result_Humidity_Array)/len(clean_result_Humidity_Array) # Calculate mean
    gc.collect()  # Delete nonsense data, Keep memory free!
    return [round(curr_Val_Temp,2),round(curr_Val_Humidity,2)]
    
### ---------- Main function -------------------
def main():
    while True:
        alarm_Pin.value(0) # Sets alarm pin to off 
        moist = plant_Monitor (sensorVCC,[left_Soil_Sensor,right_Soil_Sensor]) # Calculate the moisture level of the plants
        plant_Left_Moist_Level = moist[0]
        plant_Right_Moist_Level = moist[1]
        plants =[
            ["left",plant_Right_Moist_Level,50],
            ["right",plant_Left_Moist_Level,50]
        ]
        water_Level, watering = watering_Of_Plants(plants) # Calculates the water level in the water tank and investigates if the plants need to be watered   
        humidity_Temp = humidity_Temp_Tracker(25) # Calculates both Tempature and Humidity data
        temperature = humidity_Temp[0]
        humidity_Level = humidity_Temp[1]
        sun_Light = light_Tracker(50) # Calculates the current light level
        print("Moisture level of the Left plant: ", plant_Left_Moist_Level, "\n",
              "Moisture level of the Right plant: ", plant_Right_Moist_Level, "\n",
              "Temperature: ", temperature, "\n",
              "Humidity: ", humidity_Level, "\n",
              "Light Level: ", sun_Light, "\n",
              "Water Level: ", water_Level, "\n",
              "Watering events: ", watering)
         
        connected, wlan = connect_To_Wifi() # Try to connect to Wifi
        if connected:
            #Send data to Adafruit
            send_To_Adafruit(plant_Left_Moist_Level, "moisture-plant-1")
            plant_Left_Moist_Level=None #Delete from memory
            send_To_Adafruit(plant_Right_Moist_Level, "moisture-plant-2")
            plant_Right_Moist_Level=None #Delete from memory
            send_To_Adafruit(water_Level, "water-tank")
            water_Level=None #Delete from memory
            send_To_Adafruit(temperature, "temperature")
            temperature=None #Delete from memory
            send_To_Adafruit(humidity_Level, "humidity")
            humidity_Level=None #Delete from memory
            send_To_Adafruit(sun_Light, "sun-light")
            sun_Light=None #Delete from memory
            if len(watering) != 0: # If a watering event has been recorded
                for i in watering:
                    send_To_Adafruit(i,"watering-event")
                watering=None #Delete from memory
            wlan.disconnect() # Disconnect from WIFI
            time.sleep(1)
            if wlan.isconnected(): #If unable to disconnect
                print ("Disconnect has failed :(, It left me no choice")
                machine.reset() # Hard reset, im not allowing the pico to keep wifi on under any circumstance
            else:
                print("Great success, we have disconnected!")
                
        else: # If unable to connect to Wifi
           print("Connection was never an option :(, Data not delivered") # Data do not get uploaded or stored (Main objective is to ensure plant safety not Dashbord uplink)
           alarm_Pin.value(1) # Turn on alarm pin to indicate error
               
        deepsleep(60*60*1000)#Puts the pico into deepsleep for 60min
        
main() # Runs main function and start the program :D
